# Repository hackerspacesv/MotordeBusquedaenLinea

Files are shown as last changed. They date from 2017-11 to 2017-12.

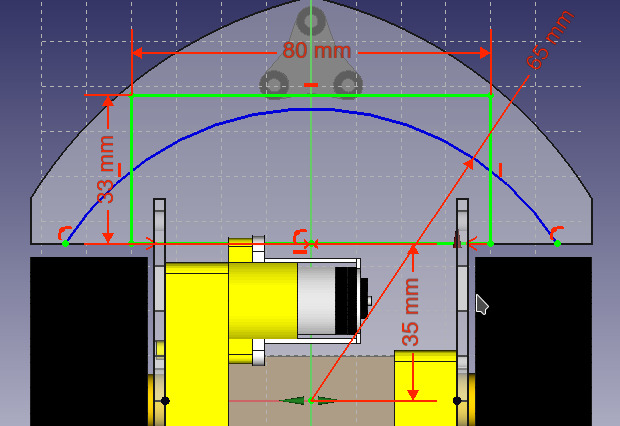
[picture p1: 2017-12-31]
Design/Notes/EsquemaSensores.jpeg

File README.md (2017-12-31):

Motor de Búsqueda en Línea
==========================
**Motor de Búsqueda en Línea** es el robot ganador del 2do Lugar en la competencia de seguidores de líneas en el ArduChallenge organizado por la <a href="https://www.facebook.com/ArduinoGuatemala/">Comunidad Arduino de Guatemala</a> el 27 de diciembre de 2017.

MBL es un proyecto de <a href="https://www.oshwa.org/definition/spanish/">Hardware Libre</a>. Todo el código fuente, archivos de diseño y documentación está disponible en este repositorio para cualquiera que desee utilizarlo o crear proyectos derivados del mismo.

Este proyecto ha sido desarrollado gracias a los aportes de Joksan Alvarado, Mario Gómez y Karla Hernández del <a href="http://hackerspace.teubi.co/">Hackerspace San Salvador</a>. El equipo del Hackerspace espera que este proyecto pueda ser replicado y utilizado para fines educativos en donde sea necesario.

¿Qué contiene este repositorio?
-------------------------------
El repositorio de MBL está organizado de la siguiente manera en las diferentes carpetas:

- **Datasheets**: Este directorio contiene las hojas técnicas de los chips utilizados en el diseño electrónico de MBL. 

- **Design**: Incluye todos los archivos de diseño mecánico y electrónico utilizados para la construcción del robot. Los archivos de diseño electrónico se pueden editar con <a href="https://www.autodesk.com/products/eagle/overview">EAGLE de Autodesk</a> y los archivos de diseño mecánico se pueden editar con <a href="https://www.freecadweb.org/">FreeCAD</a>. Esta carpeta también incluye las listas de materiales o BOM.

- **Documentation**: Esta carpeta contiene toda la documentación referente al código fuente provisto con MBL. La carpeta incluye desde notas de diseño, parámetros de configuración de protocolos de comunicación y la documentación de APIs para programadores.

- **Libraries**: Esta carpeta contienen bibliotecas de componentes utilizadas en los diseños de CAD.

- **Source**: Contiene los archivos de código fuente de la API para programadores y ejemplos básicos de uso de la misma para diferentes plataformas.

Los sub-directorios de cada carpeta podrían contener archivos *README.md* con información importante sobre el contenido de la misma.

¿Cómo utilizar MBL?
-------------------
Esta es una guía muy rápida (e incompleta) sobre cómo hacer construir y hacer funcionar a MBL.

**Hardware**:
>1. Adquiere todos los componentes especificados en el archivo *BOM.odx* en la carpeta *Design*.
>2. Corta el acrílico del chasis según los archivos de diseño provistos en la carpeta *Design/FreeCAD/SVG corte laser*.
>3. Fabrica las PCBs y ensambla según archivos de diseño en *Design/eagle*.
>4. Conecta todo según especificaciones y revisa que las conexiones eléctricas no estén cruzadas o contengan falso-contactos.

**Software**:
>1. Instala el soporte para Teensy con <a href="https://www.pjrc.com/teensy/td_download.html">Teensyduino</a>.
>2. Copia la carpeta *Source/Arduino/libraries/I32CTT* a tu carpeta de bibliotecas en Arduino.
>3. Utiliza el Sketch de ejemplo "Source/Arduino/I32CTT_PoC" para programar el robot.
>4. Utiliza el Sketch de ejemplo "Source/Arduino/I32CTT_PoC_Master" para programar controles remotos.

Si hasta este punto nada ha tomado fuego podrás utilizar MBL a través de control remoto. Modifica los ejemplos provistos para agregar funcionalidad adicional.

En la carpeta "Source/python" encontrarás también ejemplos de aplicación de control y comunitación al robot. Para ello necesitas una <a href="https://www.raspberrypi.org/">Raspberry Pi</a> y un <a href="http://openlabs.co/OSHW/Raspberry-Pi-802.15.4-radio">radio 802.15.4 de OpenLabs.co</a>.

Tecnologías utilizadas
----------------------
MBL no solo pretende ser un robot de uso específico sino una plataforma para la prueba y el desarrollo de soluciones del <a href="https://es.wikipedia.org/wiki/Internet_de_las_cosas">Internet de las Cosas (IoT)</a>. Por ello MBL hace uso de las siguientes tecnologías:

* **Procesamiento con ARM-Cortex**: <a href="https://www.arm.com/">ARM</a> es la arquitectura más utilizada en el desarrollo no solo de dispositivos móviles sino también de soluciones de IoT. MBL procesa toda la información utilizando la tarjeta electrónica <a href="https://www.pjrc.com/teensy/teensy31.html">PJRC Teensy 3.2</a> que utiliza un poderoso microcontrolador de <a href="https://www.nxp.com/products/processors-and-microcontrollers/arm-based-processors-and-mcus/kinetis-cortex-m-mcus/k-seriesperformancem4/k2x-usb/kinetis-k20-100-mhz-fu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">32-bits ARM Cortex-M4</a> corriendo a 96Mhz.
* **Comunicaciones inalámbricas con IEEE 802.15.4**: El estándar <a href="https://en.wikipedia.org/wiki/IEEE_802.15.4">IEEE 802.15.4</a> es la apuesta de <a href="https://www.ieee.org/index.html">IEEE</a> para las soluciones de IoT. Este protocolo de corto alcance y bajo ancho de banda resulta ideal para dispositivos con bajo poder de procesamiento y que requieren de un consumo mínimo de energía.
* **Control remoto y Telemetría con I32CTT**: Este protocolo desarrollado en casa por el Hackerspace San Salvador combina una especificación de mensajes cortos utilizando números enteros de 32 bits que puede ser transmitido sobre diferentes medios de comunicación. Actualmente se soportan puentes serie bluetooth e IEEE 802.15.4.

Licenciamiento
--------------
A menos que se especifique lo contrario en el archivo de código fuente, todo el código fuente incluído como parte de MBL se distribuye bajo la licencia <a href="https://www.gnu.org/licenses/gpl-3.0.en.html">GNU GPL v3.0</a>.

Todos los archivos de diseño mecánico, diseño electrónico y la documentación se distribuyen bajo la licencia Creative-Commons Attribution-ShareAlike 2.0 Generic (<a href="https://creativecommons.org/licenses/by-sa/2.0/">CC BY-SA 2.0</a>).

Archivos de documentación de terceros como hojas de datos u otros se incluyen en el repositorio sólo con fines informativos y los copyrights corresponden a sus respectivos dueños.

Todos los nombres de marcas y tecnologías mencionados en este README y documentación adjunta son propiedad de sus respectivos dueños y se utilizan solo con fines informativos.

Lo anterior implica que puedes copiar/modificar y redistribuir MBL para fines comerciales y no comerciales en tanto incluyas la información original de los autores y utilices licencias compatibles a las mencionadas anteriormente.

Información de contacto
-----------------------
Si deseas agregar funcionalidad adicional a MBL puedes enviar un *"pull request"* a este repositorio. De igual manera si encuentras algo que no funciona envíanos un *"issue"* para que podamos realizar las correcciones.

Si estás interesado en colaborar en algo más que código fuente y diseño como por ejemplo: Generar material educativo, implementar MBL en tu centro de estudios o realizar publicaciones o investigaciones tomando como base este proyecto, puedes contactarte con el equipo de desarrollo al correo electrónico <a href="mailto:info@teubi.co">info@teubi.co</a>.

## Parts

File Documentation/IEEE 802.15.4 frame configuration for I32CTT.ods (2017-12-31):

IEEE 803.15.4 frame configuration for I32CTT
Section | Field name | Size (Bits) | Size (Bytes) | Value | Meaning
FCF | Frame type | 3 | 2 | 0b001 | Data packet
 | Security enabled | 1 |  | 0b0 | No security
 | Frame pending | 1 |  | 0b0 | No pending frames
 | ACK requested | 1 |  | 0b1 | Enabled
 | PAN Id compression | 1 |  | 0b1 | Enabled
 | Reserved | 3 |  | 0b000 | Reserved
 | Destination address mode | 2 |  | 0b10 | PAN Id + Short address
 | Frame version | 2 |  | 0b01 | 802.15.4-2006 and later
 | Source address mode | 2 |  | 0b10 | PAN Id + Short address
Sequence number | Sequence number | 8 | 1 | Random start
Addressing | Destination PAN Id | 16 | 3 | User defined
 | Destination address | 16 |  | User defined
 | Source address | 16 |  | User defined
Security | Auxiliary security data | 0 | 0 | Not used
MAC Payload | MAC Payload | 8*n | n | User defined
FCS | Checksum | 16 | 2 | Calculated
Note: Related fields are shown in the same color.

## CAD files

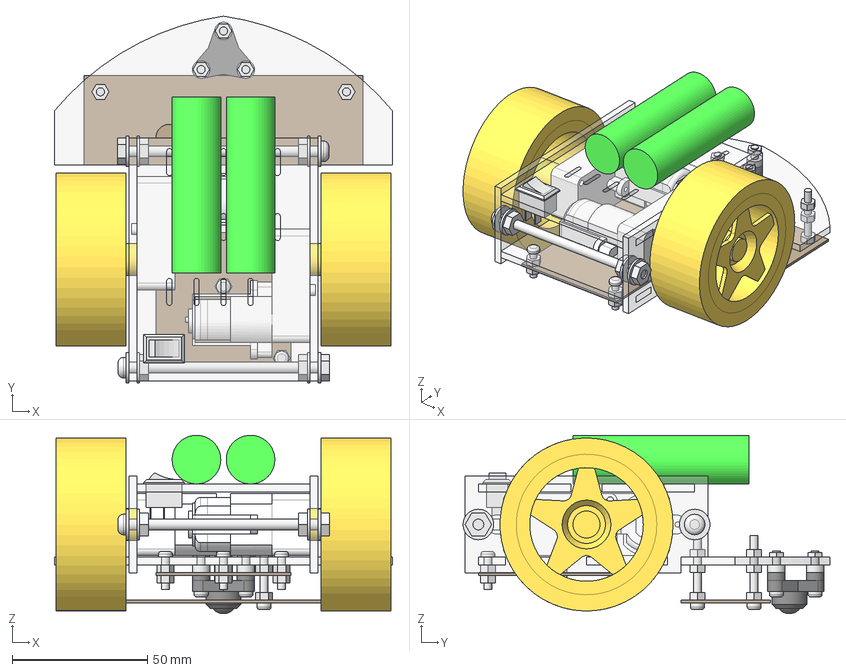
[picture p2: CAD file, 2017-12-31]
Design/FreeCAD/Motor de busqueda en linea.fcstd
125.0 x 135.6 x 66.0 mm
Tablero sensores
Tablero driver
Base
Techo
Costado izquierdo
Costado derecho
Celda izquierda
Celda derecha
Rueda izquierda
Rueda derecha
Motor izquierdo
Motor derecho
Ball caster
Soportes chassis frente
Soportes chassis atras
Soportes ball caster
Soportes driver motores
Soportes sensores
Swich poder

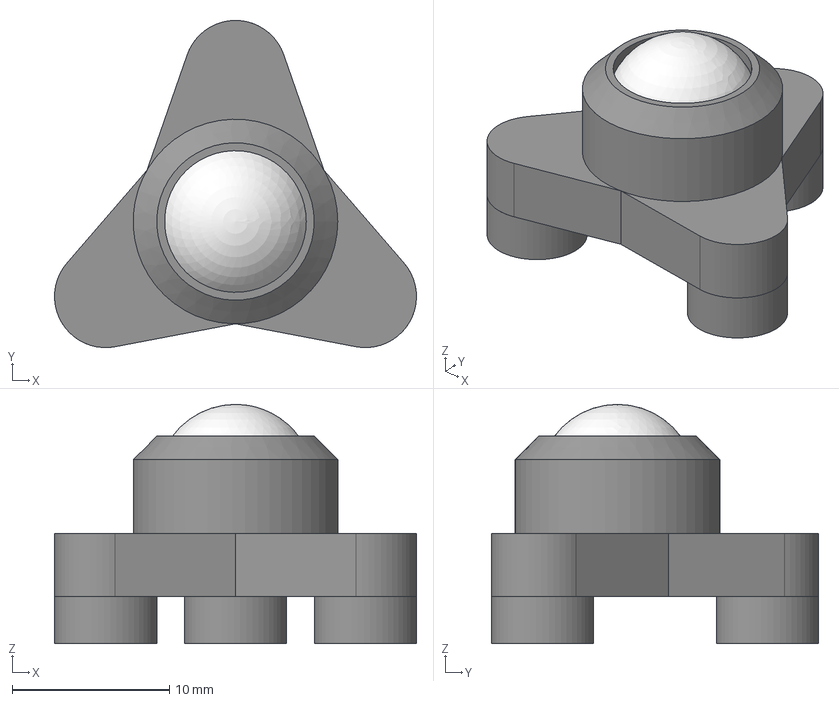
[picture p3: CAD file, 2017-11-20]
Design/FreeCAD/Partes/Ball caster.fcstd
23.0 x 20.8 x 15.2 mm

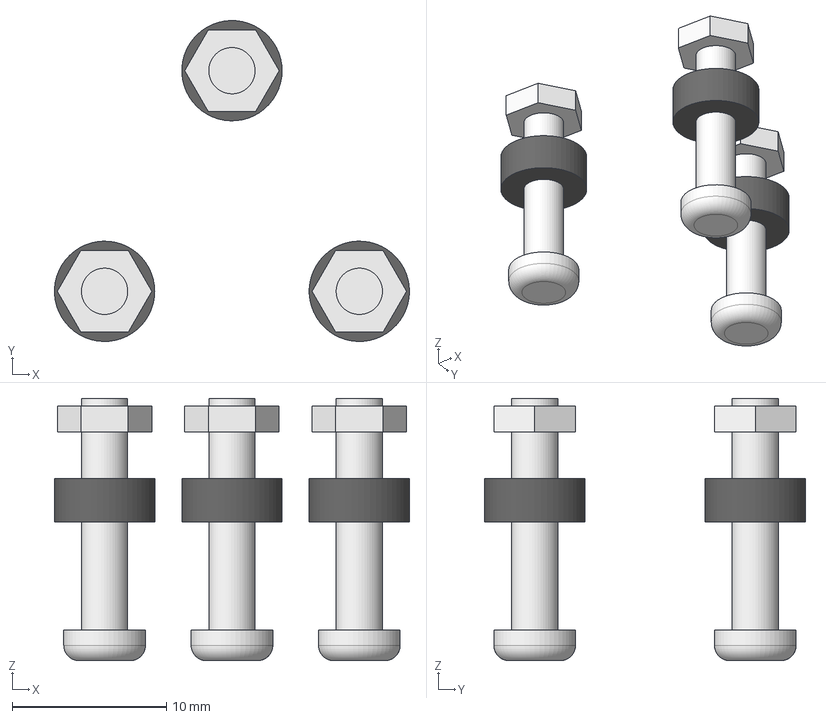
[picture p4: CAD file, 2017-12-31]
Design/FreeCAD/Partes/Soportes ball caster/Conjunto soportes ball caster.fcstd
23.0 x 20.8 x 17.0 mm
Tornillo 1
Tornillo 2
Tornillo 3
Tuerca 1
Tuerca 2
Tuerca 3
Alza 1
Alza 2
Alza 3

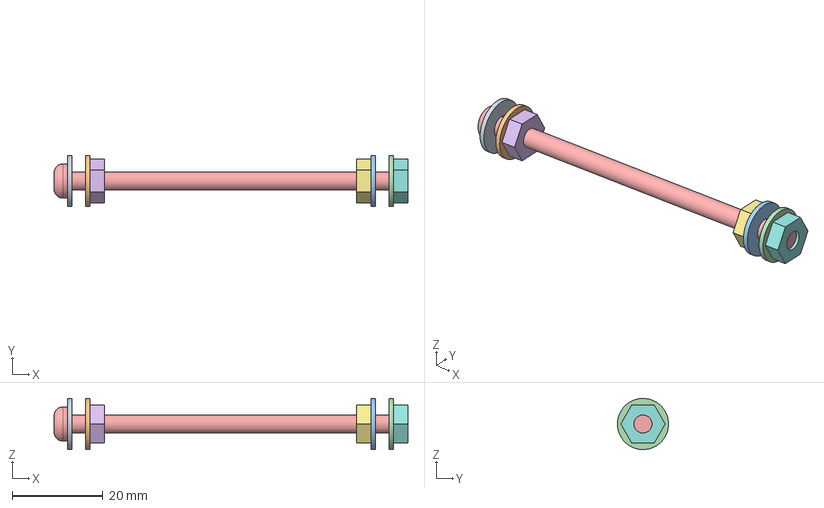
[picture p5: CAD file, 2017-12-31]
Design/FreeCAD/Partes/Soportes chassis/Conjunto soportes chassis.fcstd
78.2 x 11.3 x 11.3 mm
Arandela 1
Arandela 2
Arandela 3
Arandela 4
Tornillo
Tuerca 1
Tuerca 2
Tuerca 3

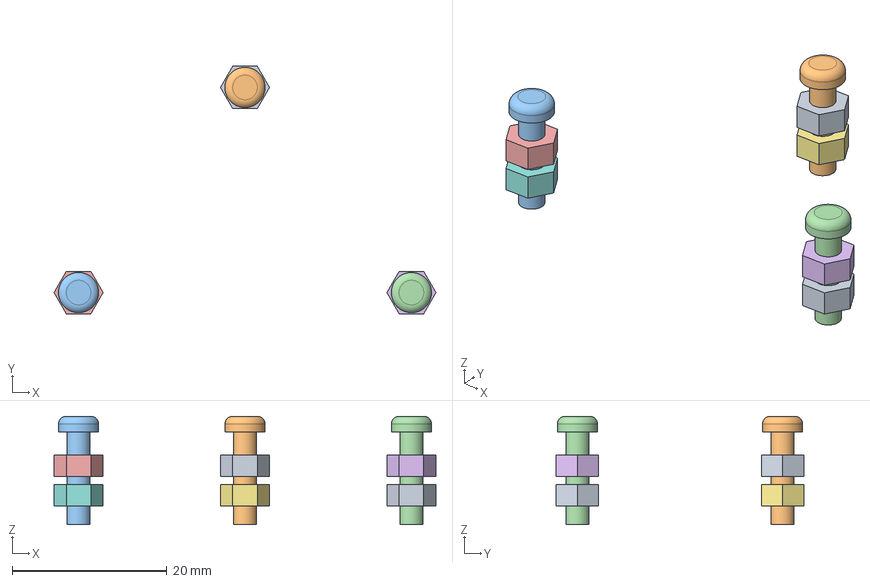
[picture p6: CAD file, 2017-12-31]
Design/FreeCAD/Partes/Soportes tableros/Conjunto soportes driver motores.fcstd
49.4 x 32.0 x 14.0 mm
Tuerca 1
Tornillo 1
Tornillo 2
Tornillo 3
Tuerca 2
Tuerca 3
Tuerca 4
Tuerca 5
Tuerca 6

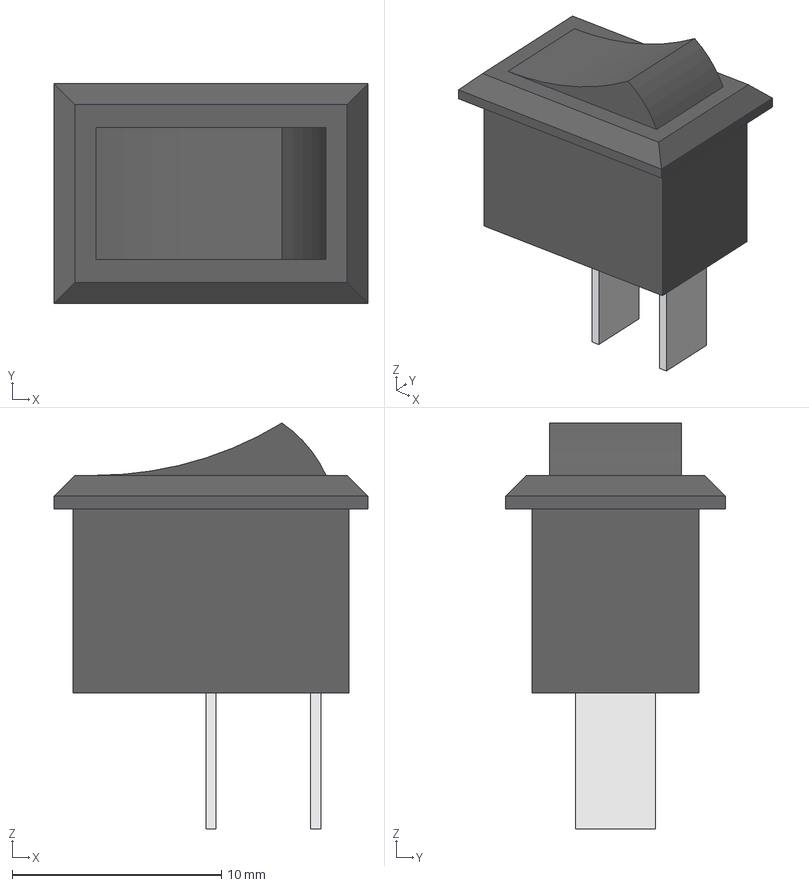
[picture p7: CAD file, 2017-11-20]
Design/FreeCAD/Partes/Rocker switch 13.6 x 9.2 mm.fcstd
15.0 x 10.5 x 19.4 mm
Base
Caratula
Balancin
Patas

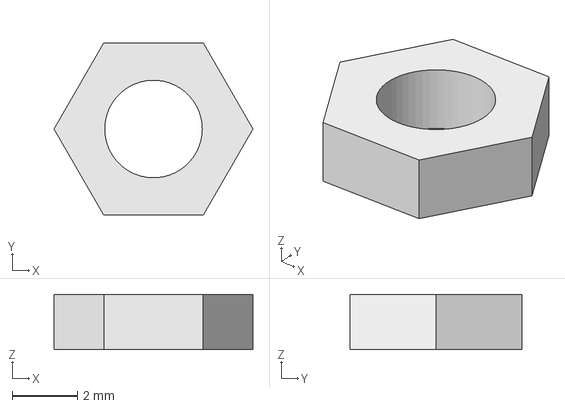
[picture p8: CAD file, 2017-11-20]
Design/FreeCAD/Partes/Soportes ball caster/Tuerca M3.fcstd
6.12 x 5.30 x 1.70 mm

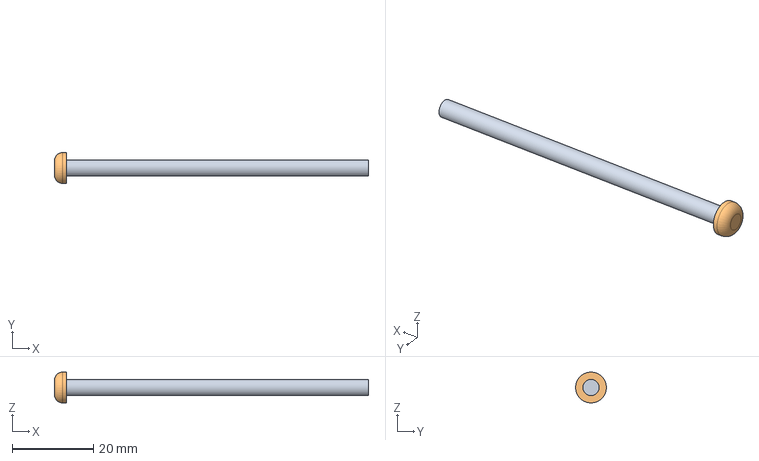
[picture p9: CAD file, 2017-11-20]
Design/FreeCAD/Partes/Soportes chassis/Tornillo 5-32 x 3 in.fcstd
77.5 x 7.59 x 7.60 mm
Rosca
Cabeza

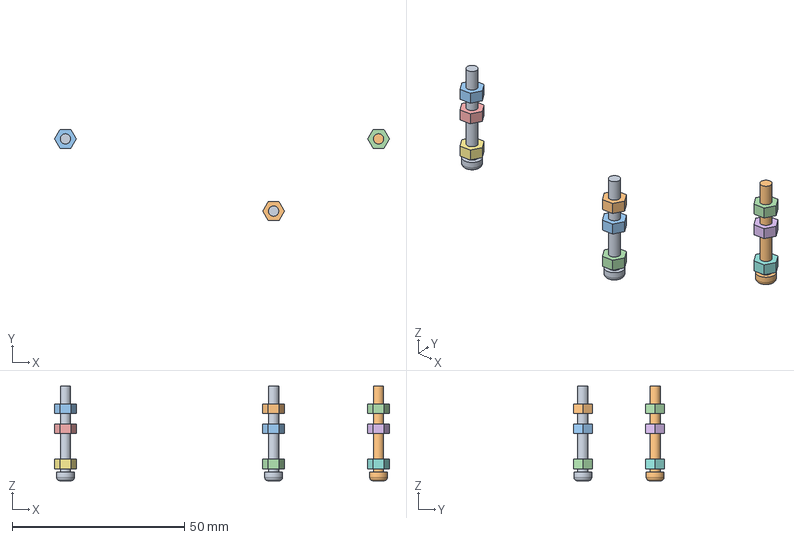
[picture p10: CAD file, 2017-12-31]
Design/FreeCAD/Partes/Soportes tableros/Conjunto soportes sensores.fcstd
97.4 x 26.5 x 27.5 mm
Tornillo 1
Tornillo 2
Tuerca 1
Tuerca 2
Tuerca 4
Tuerca 5
Tuerca 7
Tuerca 8
Tornillo 3
Tuerca 3
Tuerca 6
Tuerca 9

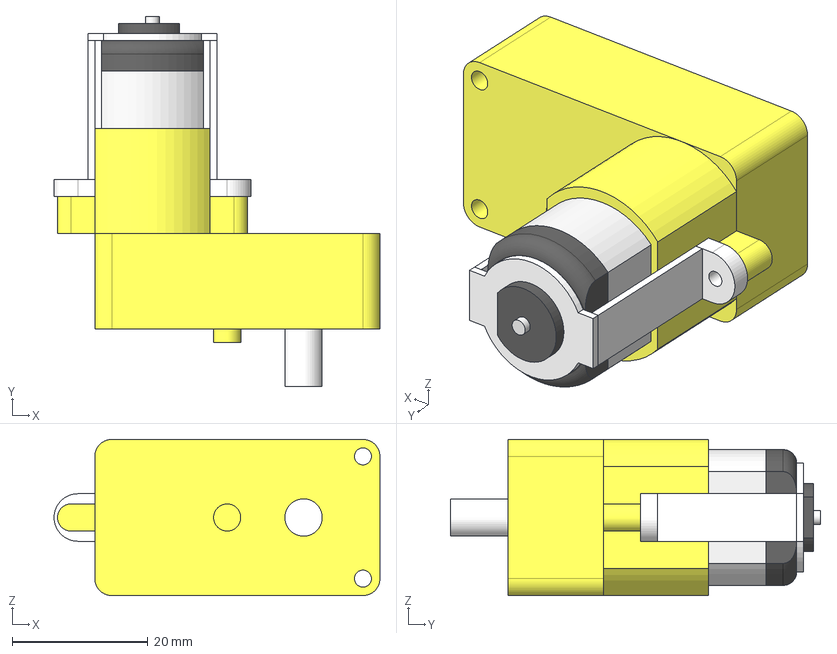
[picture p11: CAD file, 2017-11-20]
Design/FreeCAD/Partes/Motor DAGU DG02S-1P (angulo recto).fcstd
48.0 x 54.5 x 23.0 mm
Cuerpo1
Muesca
Eje
Cuerpo2
Roscas
Motor-Metal
Motor-Plastico2
Motor-Plastico1
Motor-Eje
Sujetador1
Sujetador2
Sujetador3

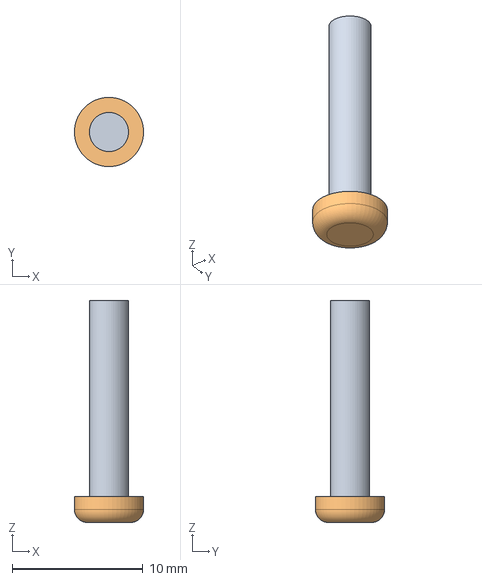
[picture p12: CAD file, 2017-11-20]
Design/FreeCAD/Partes/Soportes ball caster/Tornillo M3 x 15.fcstd
5.29 x 5.30 x 17.0 mm
Rosca
Cabeza

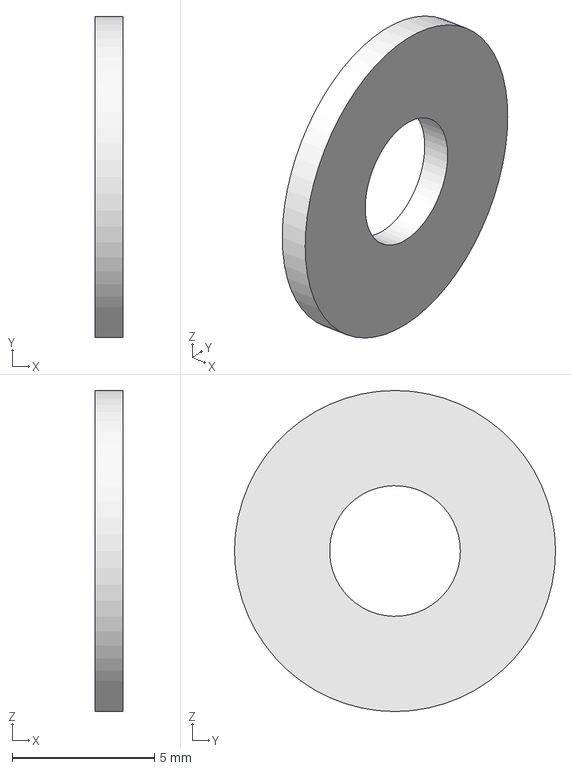
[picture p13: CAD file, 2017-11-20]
Design/FreeCAD/Partes/Soportes chassis/Arandela 5-32 in.fcstd
1.00 x 11.3 x 11.3 mm

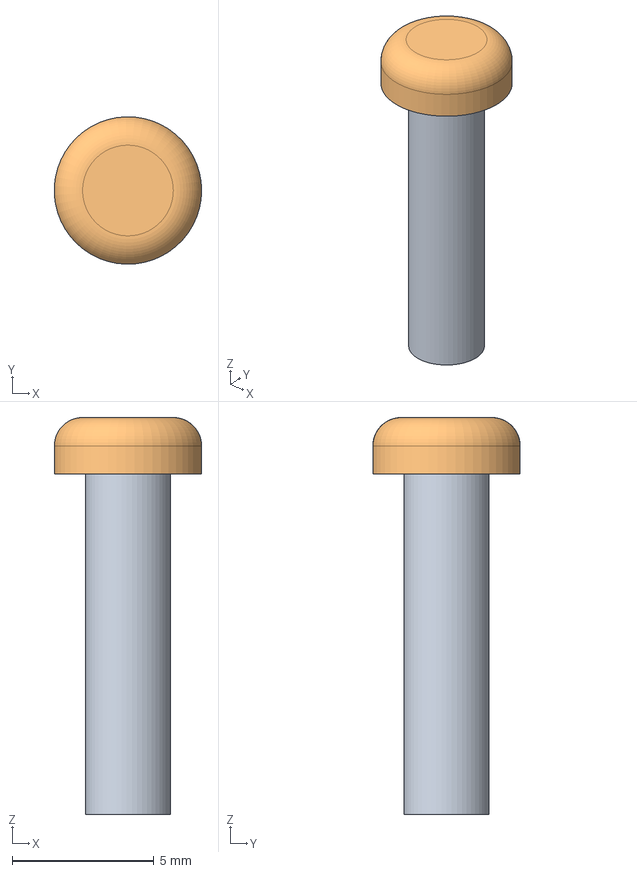
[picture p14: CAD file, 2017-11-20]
Design/FreeCAD/Partes/Soportes tableros/Tornillo 3 x 12mm.fcstd
5.20 x 5.20 x 14.0 mm
Rosca
Cabeza

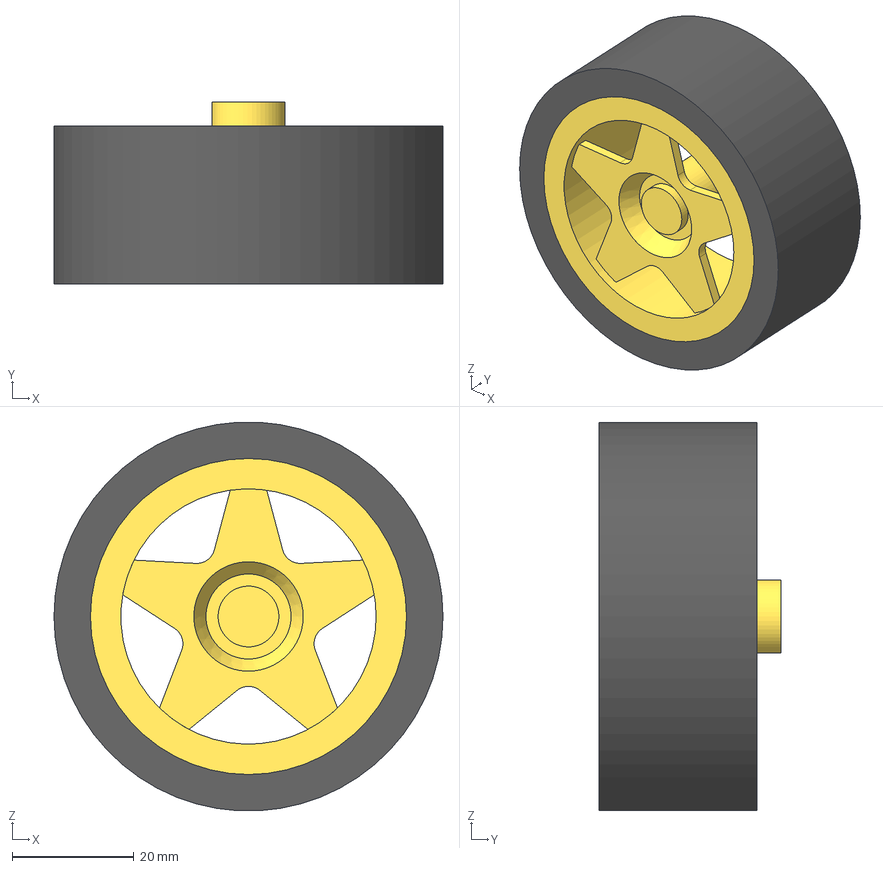
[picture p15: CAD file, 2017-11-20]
Design/FreeCAD/Partes/Rueda DAGU.fcstd
64.0 x 30.0 x 63.9 mm
Eje
Rin
Cara1
Cara2
Neumatico

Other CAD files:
Design/FreeCAD/Partes/Soportes ball caster/Alza ball caster.fcstd
Design/FreeCAD/Partes/Soportes chassis/Tuerca 5-32 in.fcstd
Design/FreeCAD/Partes/Soportes tableros/Tornillo 3 x 25mm.fcstd
Design/FreeCAD/Partes/Celda 18650.fcstd
Design/FreeCAD/Partes/Soportes tableros/Tuerca 3mm.fcstd

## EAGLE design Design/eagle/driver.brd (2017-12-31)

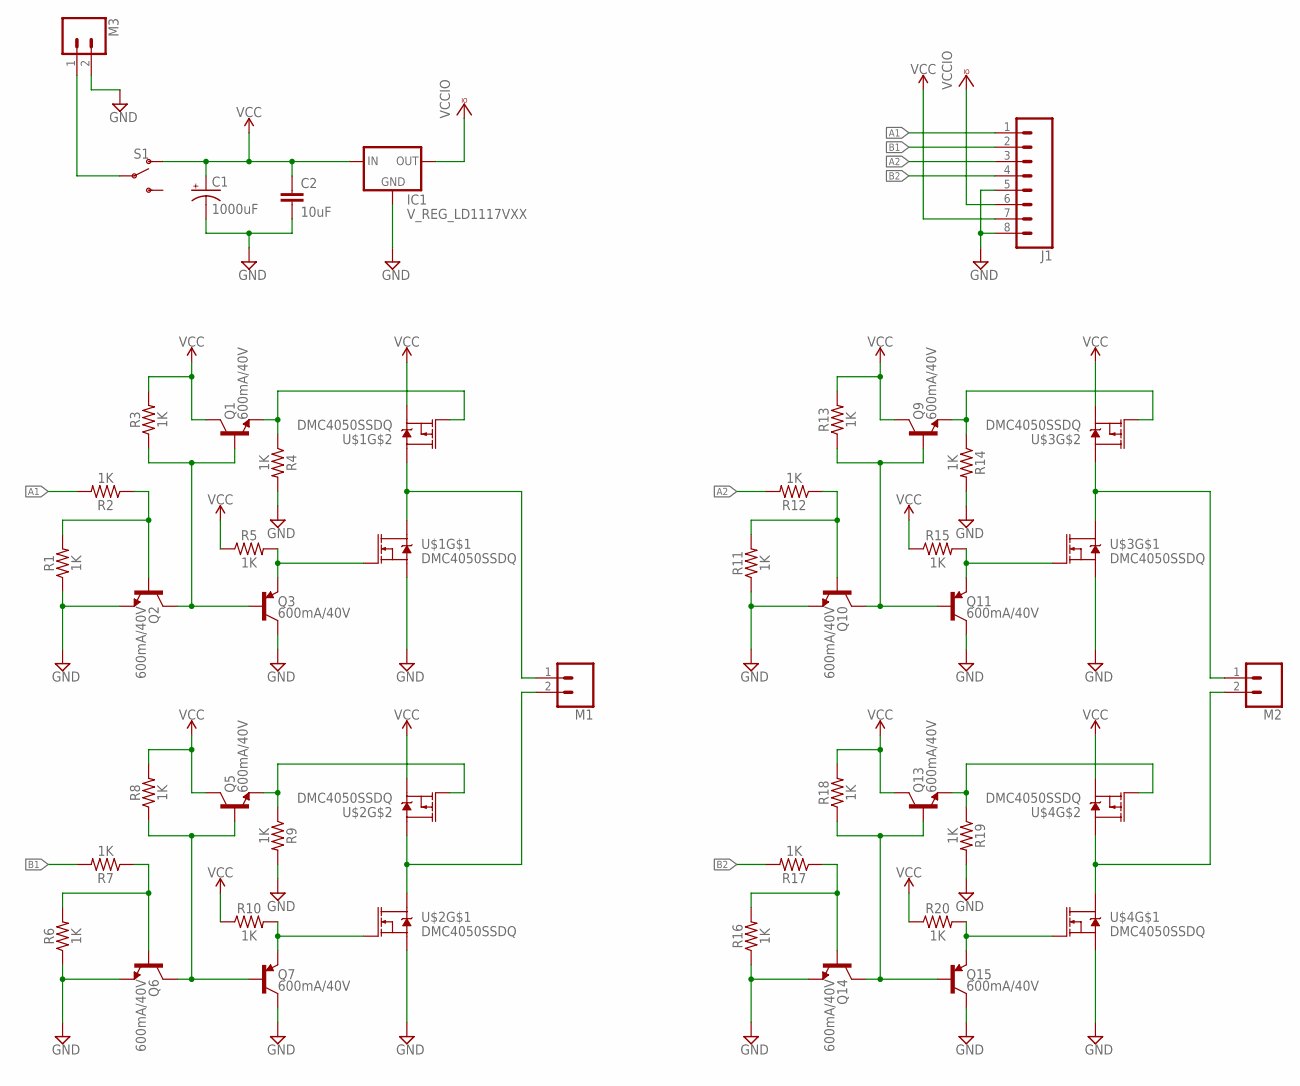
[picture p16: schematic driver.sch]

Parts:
C1: 1000uF; CPOL-RADIAL-5MM-10MM
C2: 10uF; 0805
IC1: V_REG_LD1117VXX; 78XXL
J1: CONN_08"; 1X08
M1, M2, M3: CONN_023.5MM; SCREWTERMINAL-3.5MM-2
Q1, Q2, Q3, Q5, Q6, Q7, Q9, Q10, Q11, Q13, Q14, Q15: 600mA/40V; SOT23-3
R1, R2, R3, R4, R5, R6, R7, R8, R9, R10, R11, R12, R13, R14, R15, R16, R17, R18, R19, R20: 1K; 0805
S1: SWITCH-SPDT-PTH-11.6X4.0MM; SWITCH_SPDT_PTH_11.6X4.0MM
U$1, U$2, U$3, U$4: DMC4050SSDQ; SO08

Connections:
A1: J1.1, R2.2
A2: J1.3, R12.2
B1: J1.2, R7.2
B2: J1.4, R17.2
GND: C1.-, C2.2, IC1.IN (GND), J1.5, J1.8, M3.2, Q2.2 (E), Q3.3 (C), Q6.2 (E), Q7.3 (C), Q10.2 (E), Q11.3 (C), Q14.2 (E), Q15.3 (C), R1.1, R4.2, R6.1, R9.2, R11.1, R14.2, R16.1, R19.2, U$1.1 (S), U$2.1 (S), U$3.1 (S), U$4.1 (S)
M1B: M1.2, U$2.5 (D), U$2.6 (D), U$2.7 (D), U$2.8 (D)
M1T: M1.1, U$1.5 (D), U$1.6 (D), U$1.7 (D), U$1.8 (D)
M2B: M2.2, U$4.5 (D), U$4.6 (D), U$4.7 (D), U$4.8 (D)
M2T: M2.1, U$3.5 (D), U$3.6 (D), U$3.7 (D), U$3.8 (D)
unnamed: Q2.1 (B), R1.2, R2.1
unnamed: Q1.1 (B), Q2.3 (C), Q3.1 (B), R3.1
unnamed: Q3.2 (E), R5.2, U$1.2 (G)
unnamed: Q6.1 (B), R6.2, R7.1
unnamed: Q5.1 (B), Q6.3 (C), Q7.1 (B), R8.1
unnamed: Q7.2 (E), R10.2, U$2.2 (G)
unnamed: Q1.2 (E), R4.1, U$1.4 (G)
unnamed: Q10.1 (B), R11.2, R12.1
unnamed: Q9.1 (B), Q10.3 (C), Q11.1 (B), R13.1
unnamed: Q5.2 (E), R9.1, U$2.4 (G)
unnamed: Q11.2 (E), R15.2, U$3.2 (G)
unnamed: Q9.2 (E), R14.1, U$3.4 (G)
unnamed: Q14.1 (B), R16.2, R17.1
unnamed: Q13.1 (B), Q14.3 (C), Q15.1 (B), R18.1
unnamed: Q15.2 (E), R20.2, U$4.2 (G)
unnamed: Q13.2 (E), R19.1, U$4.4 (G)
unnamed: M3.1, S1.2
VCC: C1.+, C2.1, IC1.OUT (IN), J1.7, Q1.3 (C), Q5.3 (C), Q9.3 (C), Q13.3 (C), R3.2, R5.1, R8.2, R10.1, R13.2, R15.1, R18.2, R20.1, S1.1 (O), U$1.3 (S), U$2.3 (S), U$3.3 (S), U$4.3 (S)
VCCIO: IC1.GND (OUT), J1.6

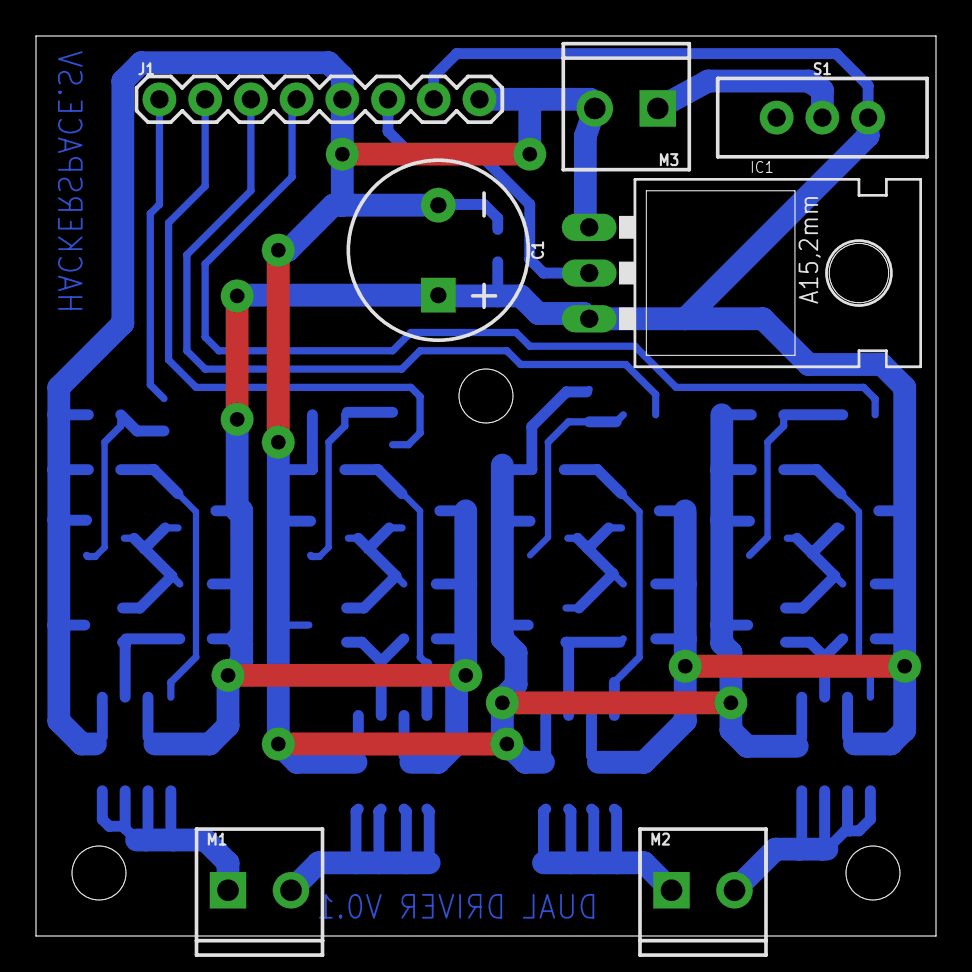
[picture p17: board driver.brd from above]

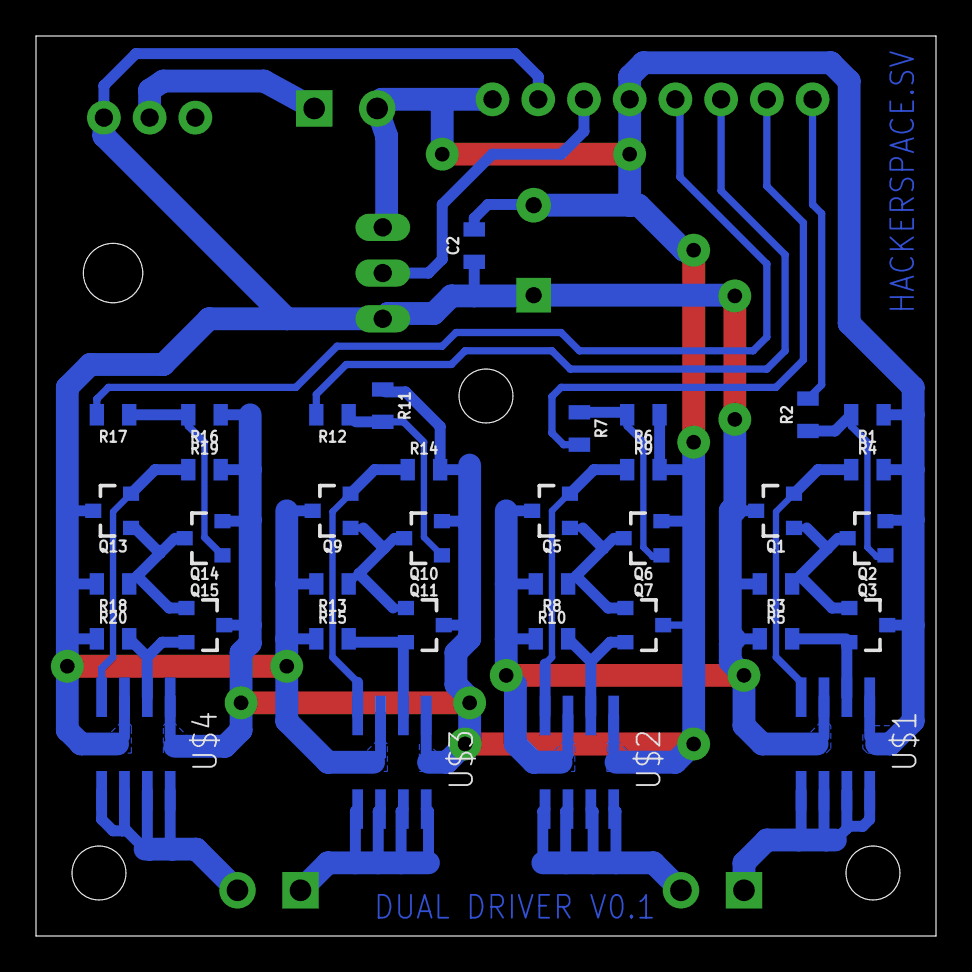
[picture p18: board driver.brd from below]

Board: 2 copper layers, 50.0 x 50.0 mm, 44 parts (37 on the bottom side), 28 nets.

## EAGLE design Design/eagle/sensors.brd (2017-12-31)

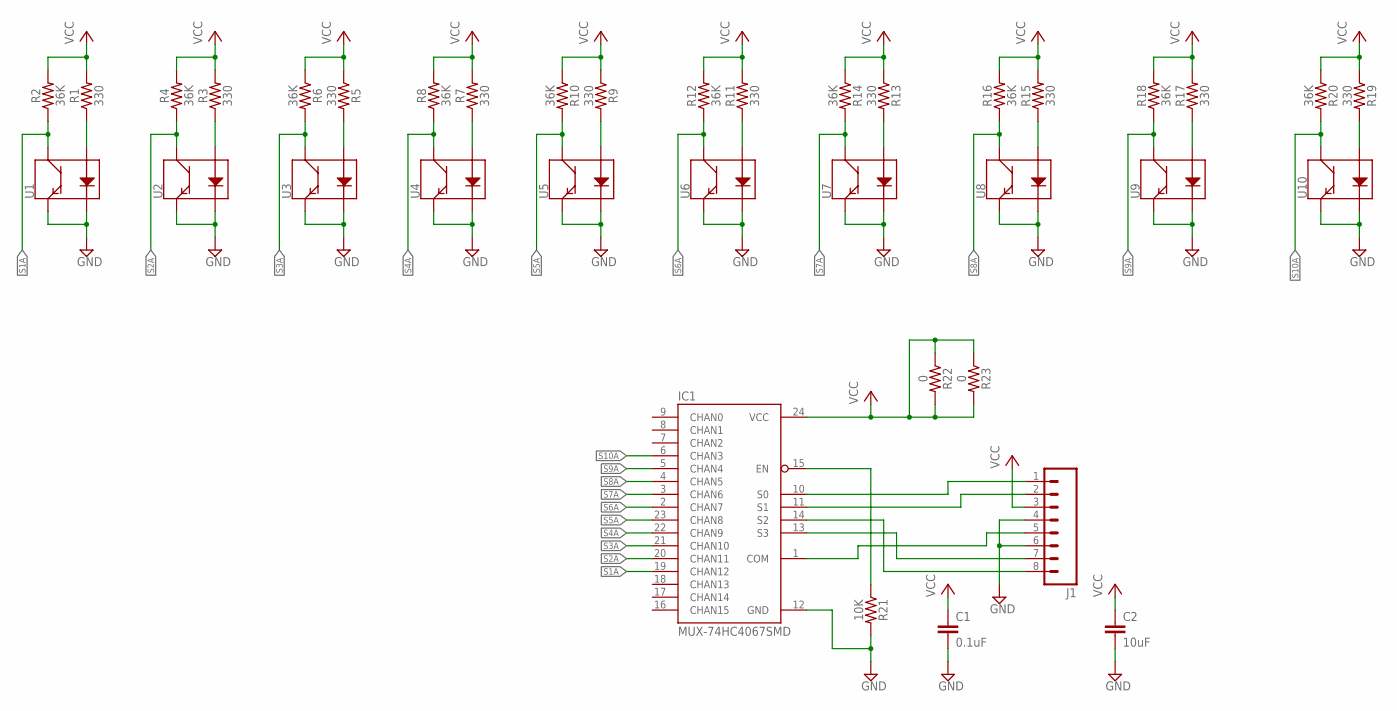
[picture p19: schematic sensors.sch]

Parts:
C1: 0.1uF; 0805
C2: 10uF; 0805
IC1: MUX-74HC4067SMD; SSOP24
J1: M08; 1X08_ROUND
R1, R3, R5, R7, R9, R11, R13, R15, R17, R19: 330; 0805
R2, R4, R6, R8, R10, R12, R14, R16, R18, R20: 36K; 0805
R21: 10K; 0805
R22, R23: 0; 0805
U1, U2, U3, U4, U5, U6, U7, U8, U9, U10: QRE1113SMD-W; QRE1113-W

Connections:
GND: C1.2, C2.2, IC1.12 (GND), J1.4, J1.6, R21.2, U1.2 (K), U1.4 (E), U2.2 (K), U2.4 (E), U3.2 (K), U3.4 (E), U4.2 (K), U4.4 (E), U5.2 (K), U5.4 (E), U6.2 (K), U6.4 (E), U7.2 (K), U7.4 (E), U8.2 (K), U8.4 (E), U9.2 (K), U9.4 (E), U10.2 (K), U10.4 (E)
unnamed: R1.1, U1.1 (A)
unnamed: IC1.13 (S3), J1.7
unnamed: R3.1, U2.1 (A)
unnamed: IC1.15 (EN), R21.1
unnamed: R5.2, U3.1 (A)
unnamed: IC1.14 (S2), J1.8
unnamed: R7.1, U4.1 (A)
unnamed: IC1.10 (S0), J1.1
unnamed: R9.2, U5.1 (A)
unnamed: IC1.11 (S1), J1.2
unnamed: R11.1, U6.1 (A)
unnamed: IC1.1 (COM), J1.5
unnamed: R13.2, U7.1 (A)
unnamed: R15.1, U8.1 (A)
unnamed: R17.1, U9.1 (A)
unnamed: R19.2, U10.1 (A)
S1A: IC1.19 (CHAN12), R2.1, U1.3 (C)
S2A: IC1.20 (CHAN11), R4.1, U2.3 (C)
S3A: IC1.21 (CHAN10), R6.2, U3.3 (C)
S4A: IC1.22 (CHAN9), R8.1, U4.3 (C)
S5A: IC1.23 (CHAN8), R10.2, U5.3 (C)
S6A: IC1.2 (CHAN7), R12.1, U6.3 (C)
S7A: IC1.3 (CHAN6), R14.2, U7.3 (C)
S8A: IC1.4 (CHAN5), R16.1, U8.3 (C)
S9A: IC1.5 (CHAN4), R18.1, U9.3 (C)
S10A: IC1.6 (CHAN3), R20.2, U10.3 (C)
VCC: C1.1, C2.1, IC1.24 (VCC), J1.3, R1.2, R2.2, R3.2, R4.2, R5.1, R6.1, R7.2, R8.2, R9.1, R10.1, R11.2, R12.2, R13.1, R14.1, R15.2, R16.2, R17.2, R18.2, R19.1, R20.1, R22.1, R22.2, R23.1, R23.2

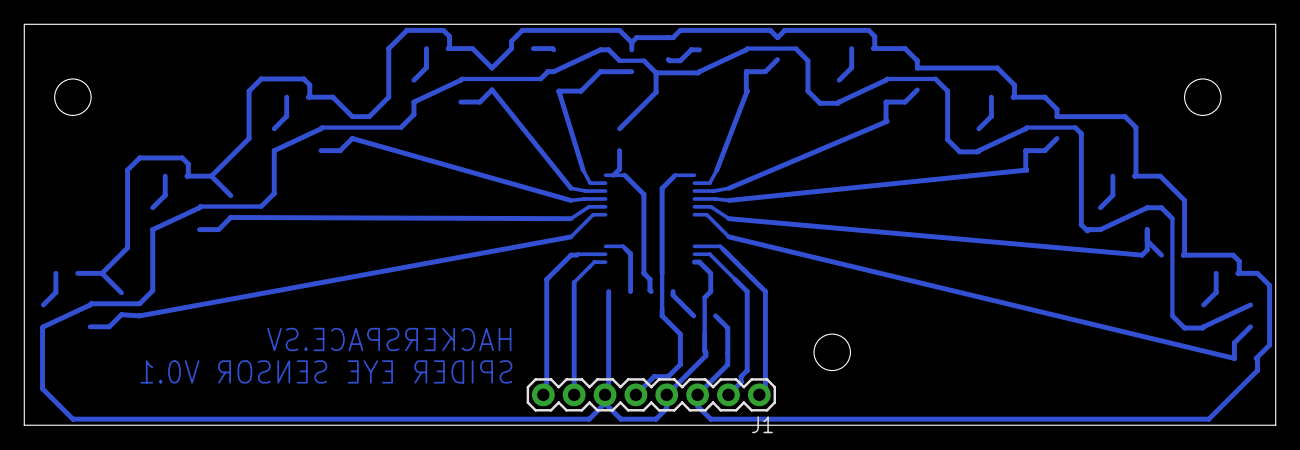
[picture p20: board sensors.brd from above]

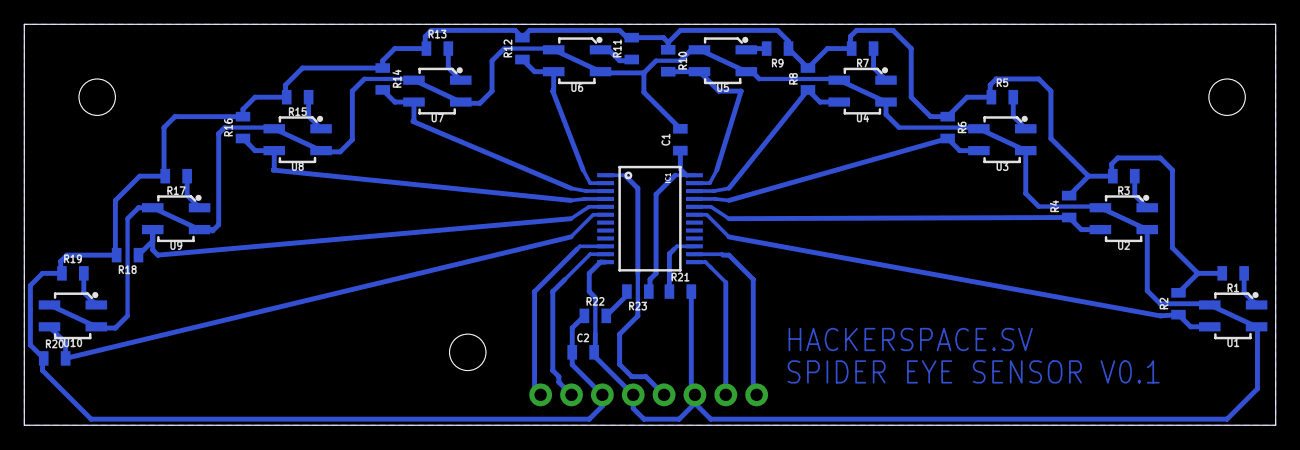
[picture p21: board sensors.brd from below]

Board: 2 copper layers, 103.0 x 33.0 mm, 37 parts (36 on the bottom side), 28 nets.

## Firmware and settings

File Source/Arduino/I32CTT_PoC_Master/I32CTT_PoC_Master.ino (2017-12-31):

/*
 * 
 * This file is part of I32CTT (Integer 32-bit Control & Telemetry Transport).
 * Copyright (C) 2017 Mario Gomez.
 * 
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
 * You should have received a copy of the GNU General Public License
 * along with I32CTT.  If not, see <http://www.gnu.org/licenses/>.
 */

/*
 * Acerca de este archivo: Este sketch es la implementación de referencia
 * para el protocolo de enteros de 32 bits para control y transporte de
 * telemetría (I32CTT).
 */
// Utilizamos string.h para facilitar el formato de salida de Serie.
#include "I32CTT.h"
#include "I32CTT_NullEndpoint.h"
#include "I32CTT_ArduinoStreamInterface.h"
#include "I32CTT_Arduino802154Interface.h"
#include "MBL_ManualEndpoint.h"
#include <string.h>

I32CTT_Controller controller(8);

//I32CTT_NullInterface myInterface;
I32CTT_ArduinoStreamInterface serialInterface(Serial);
I32CTT_Arduino802154Interface ieee802154;
I32CTT_NullEndpoint idleEndpoint(I32CTT_Endpoint::str2id("NUL"));
MBL_ManualEndpoint manualEndpoint(I32CTT_Endpoint::str2id("MAN"));

void setup() {
  while(!Serial);
  Serial.begin(9600);
  
  ieee802154.set_pan_id(0xCAFE);
  ieee802154.set_short_addr(0x0201);
  ieee802154.set_channel(C2480);
  ieee802154.set_dst_addr(0x0100);
  controller.set_interface(ieee802154);
  
  controller.add_mode_driver(idleEndpoint);
  controller.add_mode_driver(manualEndpoint);
  manualEndpoint.write(MBL_Registers::IS_ENABLED, HIGH);
  controller.enable_scheduler();
  controller.init();
  Serial.println("Running...");
}

unsigned long t_elapsed = 0;

void loop() {
  // put your main code here, to ru n repeatedly:
  controller.run();

  if((millis()-t_elapsed)>1000) {
    
    Serial.println("I'm alive");
    Serial.println("Trying to send..");
    
    controller.master.set_mode(1);
    controller.master.write_record({3, (uint32_t)0<<24});
    controller.master.try_send();
    
    //controller.master.set_mode(1);                                                                                                                                                                                                                                                                                                                                                                                                                                                                                                                                                                                                                                                                                                                                                                                                                                                                                                                                                                                                                                                                                                                                                                                                                                                                                                                                                                                                                                                                                                                                                                                                                                                                                                                                                                                                                                                                                                                                                                                                                                                                                                                                                                                                                                                                                                                                                                                                                                                                                                                                                                                                                                                                                                                                                                                                                                                                                                                                                                                                                                                                                                                                                                                                                                                                                                                                                                                                                                                                                                                                                                                                                                                                                                                                                                                                                                                                                                                                                                                                                                                                                                                                                                                                                                                                                                                                                                                                                                                                                                                                                                                                                                                                                                                                                                                                                                                                                                                                                                                                                                                                                                                                                                                                                                                                                                                                                                                                                                                                                                                                                                                                                                                                                                                                                                                                                                                                                                                                                                                                                                                                                                                                                                                                                                                                                                                                                                                                                                                                                                                                                                                                                                                                                                                                                                                                                                                                                                                                                                                                                                                                                                                                                                                                                                                                                                                                                                                                                                                                                                                                                                                                                                                                                                                                                                                                                                                                                                                                                                                                                                                                                                                                                                                                                                                                                                                                                                                                                                                                                                                                                                                                                                                                                                                                                                                                                                                                                                                                                                                                                                                                                                                                                                                                                                                                                                                                                                                                                                                                                                                                                                                                                                                                                                                                                                                                                                                                                                                                                                                                                                                                                                                                                                                                                                                                                                                                                                                                                                                                                                                                                                                                                                                                                                                                                                                                                                                                                                                                                                                                                                                                                                                                                                                                                                                                                                                                                                                                                                                                                                                                                                                                                                                                                                                                                                                                                                                                                                                                                                                                                                                                                                                                                                                                                                                                                                                                                                                                                                                                                                                                                                                                                                                                                                                                                                                                                                                                                                                                                                                                                                                                                                                                                                                                                                                                                                                                                                                                                                                                                                                                                                                                                                                                                                                                                                                                                                                                                                                                                                                                                                                                                                                                                                                                                                                                                                                                                                                                                                                                                                                                                                                                                                                                                                                                                                                                                                                                                                                                                                                                                                                                                                                                                                                                                                                                                                                                                                                                                                                                                                                                                                                                                                                                                                                                                                                                                                                                                                                                                                                                                                                                                                                                                                                                                                                                                                                                                                                                                                                                                                                                                                                                                                                                                                                                                                                                                                                                                                                                                                                                                                                                                                                                                                                                                                                                                                                                                                                                                                                                                                                                                                                                                                                                                                                                                                                                                                                                                                                                                                                                                                                                                                                                                                                                                                                                                                                                                                                                                                                                                                                                                                                                                                                                                                                                                                                                                                                                                                                                                                                                                                                       
   //controller.master.read_record(2);
    //controller.master.read_record(3); 
    //controller.master.try_send();
    
    t_elapsed = millis();
  }
  
  if(controller.master.available(CMD_AW)) {
    Serial.println("Answer received to WRITE");
  }
  if(controller.master.available(CMD_AR)) {
    Serial.println("Answer received to READ");
    for(int i=0;i<controller.master.records_available();i++) {
      I32CTT_RegData info = controller.master.read_RegData(i);
      Serial.print("Record: ");
      Serial.print(info.reg, HEX);
      Serial.print(" Data: ");
      Serial.println(info.data, HEX);
    }
  }
}

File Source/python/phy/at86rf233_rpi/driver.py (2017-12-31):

import spidev
import time

class driver_at86rf233:
  #Estados de interes del radio, usados en la funcion de cambio de estado
  ESTADO_RX_AACK = 0
  ESTADO_TX_ARET = 1

  #Clase vacia usada como contenedor de constantes
  class clase_vacia:
    pass

  #Pines del radio (segun numeracion de tablero)
  __pin = clase_vacia()
  __pin.IRQ    = 16
  __pin.RST    = 18
  __pin.SLP_TR = 22

  #Comandos de bus SPI para el radio
  __cmd_spi = clase_vacia()
  __cmd_spi.REG_READ   = 0x80
  __cmd_spi.REG_WRITE  = 0xC0
  __cmd_spi.FB_READ    = 0x20
  __cmd_spi.FB_WRITE   = 0x60
  __cmd_spi.SRAM_READ  = 0x00
  __cmd_spi.SRAM_WRITE = 0x40

  #Registro TRX_STATUS
  __TRX_STATUS                                         = clase_vacia()
  __TRX_STATUS.addr                                    = 0x01
  __TRX_STATUS.TRX_STATUS                              = clase_vacia()
  __TRX_STATUS.TRX_STATUS.mask                         = 0x1F
  __TRX_STATUS.TRX_STATUS.P_ON                         = 0x00
  __TRX_STATUS.TRX_STATUS.BUSY_RX                      = 0x01
  __TRX_STATUS.TRX_STATUS.BUSY_TX                      = 0x02
  __TRX_STATUS.TRX_STATUS.RX_ON                        = 0x06
  __TRX_STATUS.TRX_STATUS.TRX_OFF                      = 0x08
  __TRX_STATUS.TRX_STATUS.PLL_ON                       = 0x09
  __TRX_STATUS.TRX_STATUS.SLEEP                        = 0x0F
  __TRX_STATUS.TRX_STATUS.PREP_DEEP_SLEEP              = 0x10
  __TRX_STATUS.TRX_STATUS.BUSY_RX_AACK                 = 0x11
  __TRX_STATUS.TRX_STATUS.BUSY_TX_ARET                 = 0x12
  __TRX_STATUS.TRX_STATUS.RX_AACK_ON                   = 0x16
  __TRX_STATUS.TRX_STATUS.TX_ARET_ON                   = 0x19
  __TRX_STATUS.TRX_STATUS.STATE_TRANSITION_IN_PROGRESS = 0x1F

  #Registro TRX_STATE
  __TRX_STATE                                    = clase_vacia()
  __TRX_STATE.addr                               = 0x02
  __TRX_STATE.TRX_CMD                            = clase_vacia()
  __TRX_STATE.TRX_CMD.mask                       = 0x1F
  __TRX_STATE.TRX_CMD.NOP                        = 0x00
  __TRX_STATE.TRX_CMD.TX_START                   = 0x02
  __TRX_STATE.TRX_CMD.FORCE_TRX_OFF              = 0x03
  __TRX_STATE.TRX_CMD.FORCE_PLL_ON               = 0x04
  __TRX_STATE.TRX_CMD.RX_ON                      = 0x06
  __TRX_STATE.TRX_CMD.TRX_OFF                    = 0x08
  __TRX_STATE.TRX_CMD.PLL_ON                     = 0x09
  __TRX_STATE.TRX_CMD.PREP_DEEP_SLEEP            = 0x10
  __TRX_STATE.TRX_CMD.RX_AACK_ON                 = 0x16
  __TRX_STATE.TRX_CMD.TX_ARET_ON                 = 0x19
  __TRX_STATE.TRAC_STATUS                        = clase_vacia()
  __TRX_STATE.TRAC_STATUS.mask                   = 0xE0
  __TRX_STATE.TRAC_STATUS.SUCCESS                = 0x00 
  __TRX_STATE.TRAC_STATUS.SUCCESS_DATA_PENDING   = 0x20
  __TRX_STATE.TRAC_STATUS.SUCCESS_WAIT_FOR_ACK   = 0x40
  __TRX_STATE.TRAC_STATUS.CHANNEL_ACCESS_FAILURE = 0x60
  __TRX_STATE.TRAC_STATUS.NO_ACK                 = 0xA0
  __TRX_STATE.TRAC_STATUS.INVALID                = 0xE0

  #Registro PHY_CC_CCA
  __PHY_CC_CCA                  = clase_vacia()
  __PHY_CC_CCA.addr             = 0x08
  __PHY_CC_CCA.CHANNEL          = clase_vacia()
  __PHY_CC_CCA.CHANNEL.mask     = 0x1F
  __PHY_CC_CCA.CCA_MODE         = clase_vacia()
  __PHY_CC_CCA.CCA_MODE.mask    = 0x60
  __PHY_CC_CCA.CCA_MODE.Mode_3a = 0x00
  __PHY_CC_CCA.CCA_MODE.Mode_1  = 0x20
  __PHY_CC_CCA.CCA_MODE.Mode_2  = 0x40
  __PHY_CC_CCA.CCA_MODE.Mode_3b = 0x60
  __PHY_CC_CCA.CCA_REQUEST      = clase_vacia()
  __PHY_CC_CCA.CCA_REQUEST.mask = 0x80

  #Registro TRX_CTRL_2
  __TRX_CTRL_2                      = clase_vacia()
  __TRX_CTRL_2.addr                 = 0x0C
  __TRX_CTRL_2.RX_SAFE_MODE         = clase_vacia()
  __TRX_CTRL_2.RX_SAFE_MODE.mask    = 0x80
  __TRX_CTRL_2.OQPSK_SCRAM_EN       = clase_vacia()
  __TRX_CTRL_2.OQPSK_SCRAM_EN.mask  = 0x20
  __TRX_CTRL_2.OQPSK_DATA_RATE      = clase_vacia()
  __TRX_CTRL_2.OQPSK_DATA_RATE.mask = 0x07

  #Registro IRQ_MASK
  __IRQ_MASK                        = clase_vacia()
  __IRQ_MASK.addr                   = 0x0E
  __IRQ_MASK.IRQ_0_PLL_LOCK         = clase_vacia()
  __IRQ_MASK.IRQ_0_PLL_LOCK.mask    = 0x01
  __IRQ_MASK.IRQ_1_PLL_UNLOCK       = clase_vacia()
  __IRQ_MASK.IRQ_1_PLL_UNLOCK.mask  = 0x02
  __IRQ_MASK.IRQ_2_RX_START         = clase_vacia()
  __IRQ_MASK.IRQ_2_RX_START.mask    = 0x04
  __IRQ_MASK.IRQ_3_TRX_END          = clase_vacia()
  __IRQ_MASK.IRQ_3_TRX_END.mask     = 0x08
  __IRQ_MASK.IRQ_4_CCA_ED_DONE      = clase_vacia()
  __IRQ_MASK.IRQ_4_CCA_ED_DONE.mask = 0x10
  __IRQ_MASK.IRQ_5_AMI              = clase_vacia()
  __IRQ_MASK.IRQ_5_AMI.mask         = 0x20
  __IRQ_MASK.IRQ_6_TRX_UR           = clase_vacia()
  __IRQ_MASK.IRQ_6_TRX_UR.mask      = 0x40
  __IRQ_MASK.IRQ_7_BAT_LOW          = clase_vacia()
  __IRQ_MASK.IRQ_7_BAT_LOW.mask     = 0x80

  #Registro IRQ_STATUS
  __IRQ_STATUS                        = clase_vacia()
  __IRQ_STATUS.addr                   = 0x0F
  __IRQ_STATUS.IRQ_0_PLL_LOCK         = clase_vacia()
  __IRQ_STATUS.IRQ_0_PLL_LOCK.mask    = 0x01
  __IRQ_STATUS.IRQ_1_PLL_UNLOCK       = clase_vacia()
  __IRQ_STATUS.IRQ_1_PLL_UNLOCK.mask  = 0x02
  __IRQ_STATUS.IRQ_2_RX_START         = clase_vacia()
  __IRQ_STATUS.IRQ_2_RX_START.mask    = 0x04
  __IRQ_STATUS.IRQ_3_TRX_END          = clase_vacia()
  __IRQ_STATUS.IRQ_3_TRX_END.mask     = 0x08
  __IRQ_STATUS.IRQ_4_CCA_ED_DONE      = clase_vacia()
  __IRQ_STATUS.IRQ_4_CCA_ED_DONE.mask = 0x10
  __IRQ_STATUS.IRQ_5_AMI              = clase_vacia()
  __IRQ_STATUS.IRQ_5_AMI.mask         = 0x20
  __IRQ_STATUS.IRQ_6_TRX_UR           = clase_vacia()
  __IRQ_STATUS.IRQ_6_TRX_UR.mask      = 0x40
  __IRQ_STATUS.IRQ_7_BAT_LOW          = clase_vacia()
  __IRQ_STATUS.IRQ_7_BAT_LOW.mask     = 0x80

  #Registros SHORT_ADDR_0 y SHORT_ADDR_1
  __SHORT_ADDR_0      = clase_vacia()
  __SHORT_ADDR_0.addr = 0x20
  __SHORT_ADDR_1      = clase_vacia()
  __SHORT_ADDR_1.addr = 0x21

  #Registros PAN_ID_0 y PAN_ID_1
  __PAN_ID_0      = clase_vacia
  __PAN_ID_0.addr = 0x22
  __PAN_ID_1      = clase_vacia()
  __PAN_ID_1.addr = 0x23

  def __init__(self, gpio):
    #Crea el objeto del bus SPI0, linea CS0 y lo inicializa a 1MHz
    self.__spi = spidev.SpiDev()
    self.__spi.open(0,0)
    self.__spi.max_speed_hz = 1000000

    #Configura los pines de I/O usados para el radio
    self.__gpio = gpio
    self.__gpio.setmode(self.__gpio.BOARD)
    self.__gpio.setup(self.__pin.IRQ, self.__gpio.IN)#, pull_up_down=self.__gpio.PUD_UP);
    self.__gpio.setup(self.__pin.RST, self.__gpio.OUT)
    self.__gpio.setup(self.__pin.SLP_TR, self.__gpio.OUT);

    #Llama a la rutina de inicializacion del radio
    self.__reset()

    #Habilita la proteccion dinamica del frame buffer, para evitar que los paquetes recibidos sean
    #sobre escritos hasta que sean leidos.
    self.__escr_campo_modo_seguro_rx(True)
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

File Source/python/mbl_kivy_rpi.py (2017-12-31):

from kivy.app import App
from kivy.clock import Clock

from mbl_kivy.mbl_ventana_principal import VentanaPrincipal

#gpio = None
#from phy.nulo.driver import driver_phy_nulo as driver_phy
#from mac.nulo.driver import driver_mac_nulo as driver_mac
import RPi.GPIO as gpio
from phy.at86rf233_rpi.driver import driver_at86rf233 as driver_phy
from mac.ieee802154.driver import driver_ieee802154 as driver_mac
from i32ctt.driver import driver_i32ctt

direccion_mbl = 0x0100
ep_manu = 0
ep_manu_x = 2
ep_manu_y = 3

#Clase para la aplicacion
class MyApp(App):
  def build(self):
    self.ventana = VentanaPrincipal(i32ctt, direccion_mbl, (0, 1, 2))
    return self.ventana

#Funcion de actualizacion periodica
def actualizacion_periodica(dt):
  app.ventana.actualizacion_periodica()

if __name__ == '__main__':
  phy = driver_phy(gpio)
  mac = driver_mac(phy)
  i32ctt = driver_i32ctt(mac)

  mac.escr_config_red(canal=26, pan_id=0xCAFE, dir_corta=0x0200)

  Clock.schedule_interval(actualizacion_periodica, 0.01)

  try:
    app = MyApp()
    app.run()
  finally:
    if gpio and gpio.cleanup:
      gpio.cleanup()

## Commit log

2017-11-02 Cambiando licencia gpl2 por gpl3 luego de platicas interesantes.
2017-11-02 Agregando el archivo de lectura de la gpl3, leelo esta interesante.
2017-11-13 Agregado circuito y PCB driver de motor.
    [driver.brd, driver.sch]
2017-11-13 Correcciones al PCB
    [driver.brd]
2017-11-13 Removidos vias sobrepuestos automaticamente.
    [driver.brd]
2017-11-13 Agregada distribucion PCB sensores
    [sensors.brd, sensors.sch]
2017-11-15 Finished sensor PCB + Analog MUX
    [sensors.brd, sensors.sch]
2017-11-15 Fixed missing COM line from analog MUX
    [sensors.brd, sensors.sch]
2017-11-18 Agregados ajustes en PCB para fotosensibilizada.
    [driver.brd, sensors.brd]
2017-11-19 Agregadas correcciones en PCB
    [driver.brd, driver.sch, sensors.brd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]
2017-11-20 [CAD] Agregados todos los archivos de FreeCAD y archivos de corte laser en SVG.
    [Alza ball caster.fcstd, Arandela 5-32 in.fcstd, Ball caster.fcstd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]
2017-11-20 [Documentacion] Agregadas hojas de datos de BJT NPN, Mux analogo y sensor reflectivo.
2017-11-25 Archivos de FreeCAD movidos a carpeta Design
    [Alza ball caster.fcstd, Arandela 5-32 in.fcstd, Ball caster.fcstd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]
2017-11-25 Agregado Sketch para prueba de sensor.
2017-11-25 Corregida nota de Copyright en PruebaSensordeLinea.
2017-11-28 Agregado Null driver telemetria.
2017-11-28 Agregada interfaz de red nula.
2017-11-29 Agregado parser de protocolo. --No probado--
2017-11-30 Agregado transporte Stream para Arduino
2017-12-02 Arreglado bug de alojamiento de memoria.
    [I32CTT_PoC.ino]
2017-12-10 Agregados cambios en la API.
2017-12-11 Varios cambios en API. Stub para AT86RF233.
2017-12-11 Engrosado el acrilico a 3mm y agregado espacio vertical para los motores dentro del chassis.
    [Conjunto soportes ball caster.fcstd, Conjunto soportes chassis.fcstd, Conjunto soportes driver motores.fcstd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]
2017-12-16 Agregada maquina de estados radio 802.15.4
2017-12-17 Agregado soporte para IEEE 802.15.4 en Arduino.
2017-12-17 Agregados los archivos de codigo fuente con soporte para Raspberry Pi.
2017-12-18 Agregada respuesta automatica a origen. Corregido error en generacion de paquete en master. Cambios minimos en API de Interfaz de red
    [I32CTT_PoC.ino, MBL_ManualEndpoint.cpp, PruebaSensordeLinea.ino]
2017-12-18 Agregada documentacion FCF para IEEE 802.15.4
    [IEEE 802.15.4 frame configuration for I32CTT.ods]
2017-12-18 Removida hoja de datos duplicada.
2017-12-22 Agregado soporte de introspeccion de I32CTT
2017-12-23 Completado el programa de control para raspberry pi.
    - Agregado soporte de descodificacion de tramas 802.15.4
    - Implementado el protocolo i32ctt
    - Implementada la aplicacion de kivy para raspberry pi (control remoto)
2017-12-23 Agregado README para RC-1.
2017-12-26 Ampliado el codigo de gui para MBL en el port de raspberry pi.
    - [gui] Reestructurado el codigo, mejorando modularidad.
    - [gui] Implementado endpoint de control automatico.
    - [i32ctt] Ajustado el timeout de los paquetes.
    - [MAC], [PHY] Implementados los drivers nulos para MAC y PHY.
    - [PHY], [BUGFIX] Corregida la forma en que se calcula el timeout para comunicacion SPI.
    [driver.py, i32ctt_test.py, mbl_kivy_rpi.py]
2017-12-28 Corregido codigo prueba sensores. Corregido bug reportado por Joksan en endpoint I32CTT.
    [PruebaSensordeLinea.ino]
2017-12-28 Completada la interfaz grafica del endpoint automatico.
2017-12-28 Cambios para mostar en el hangout luego del arduchallege
2017-12-31 Aumentada velocidad de SPI a 1Mbps

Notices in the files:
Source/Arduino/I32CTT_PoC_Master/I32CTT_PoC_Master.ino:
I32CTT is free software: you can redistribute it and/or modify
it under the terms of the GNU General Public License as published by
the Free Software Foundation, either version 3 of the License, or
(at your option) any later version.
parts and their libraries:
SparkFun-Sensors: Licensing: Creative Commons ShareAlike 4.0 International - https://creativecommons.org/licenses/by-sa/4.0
